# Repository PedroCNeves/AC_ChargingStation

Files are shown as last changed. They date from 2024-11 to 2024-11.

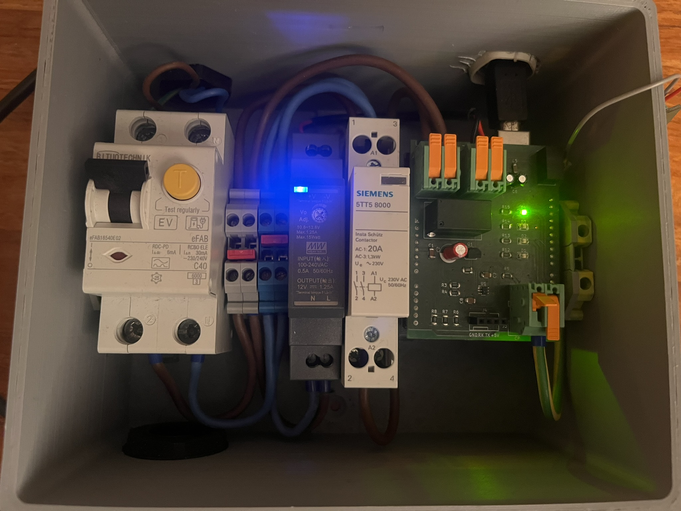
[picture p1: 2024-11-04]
EVSE_Photo.JPEG

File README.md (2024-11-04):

This is a repository for a learning and development project (not a finished product).
This repository contains:
- Code for Arduino Uno to work as an EV AC Charging Station.
- KiCAD Schematic and PCB of a Shield for Arduino Uno to make the hardware for an EV AC Charging Station.
- Gerber files to fabricate the Shield.
- BOM to assemble the Shield.

Instructions to execute this learning project: https://www.udemy.com/course/electric-vehicle-charging-from-theory-to-practice/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

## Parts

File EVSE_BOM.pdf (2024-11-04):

Charging Station Components Link to Product Quantity Unit Cost Sum Cost Box with DIN rail 1 32 32
RCBO https://ecoharmony.co.uk/collecti 1 61 61 Arduino Uno https://store.arduino.cc/products/1 30 30 Charging Station shield for Arduino 1 30 30 DIN Rail adapter for Arduino Uno 1 5 5 Contactor 1P, 20 A https://www.reichelt.nl/nl/nl/insta-1 22 22 DIN Rail Power Supply +12 V https://www.reichelt.nl/nl/nl/schak 1 12 12 Wire 2.5 mm2, blue https://www.elektramat.nl/heluka 1 0.5 0.5 Wire 2.5 mm2, brown https://www.elektramat.nl/heluka 1 0.5 0.5 Wire 2.5 mm2, yellow/green https://www.elektramat.nl/heluka 1 0.5 0.5 Ferrule terminals https://www.elektramat.nl/weidm 25 0.1 2.5 DIN Connectors PE https://www.elektramat.nl/phoeni 2 4 8 DIN Connector Blue https://www.elektramat.nl/phoeni 2 1.2 2.4 DIN Connector Grey https://www.elektramat.nl/phoeni 2 1.2 2.4 Shunt for DIN connectors https://www.elektramat.nl/phoeni 2 0.5 1 End cap for DIN connectors https://www.elektramat.nl/phoeni 2 0.6 1.2 Grommet M20 https://www.elektramat.nl/jacob-w 2 0.6 1.2 Grommet nut M20 https://www.elektramat.nl/jacob-w 2 0.1 0.2 Installation cable 3G2.5 https://www.elektramat.nl/neopre 3 2.4 7.2 Type-2 vehicle connector with cable https://evchargeplus.com/produc 1 170 170
| Total 389.6

Arduino Uno Shield PCB Components (not counting the PCB itself)
Component | Reference in PCB | Link to Product | Quantity | Unit Cost | Sum Cost
Total | 16.595
Operational Amplifier TLV1805DBVR | U1 | 1 | 0.81 | 0.81
Power Supply NKE1212SC | U2 | 1 | 6.2 | 6.2
0.1 uF Capacitors | C1,C3,C5,C7,C8 | 5 | 0.093 | 0.465
10 uF Capacitors | C4,C6 | 2 | 0.12 | 0.24
100 uF Capacitor | C2 | 1 | 0.13 | 0.13
LEDs | D1,D2,D3,D4 | 4 | 0.2 | 0.8
Transistor | Q1 | 1 | 0.4 | 0.4
Relays | K1 | 1 | 1.66 | 1.66
Power Connectors | J1,J2,J3 | 3 | 1.31 | 3.93
Connector, serial coms | J4 | 1 | 0.31 | 0.31
Resistors 1k | R2,R5,R12,R13,R14,R15 | 6 | 0.09 | 0.54
Resistors 100k | R3,R4,R8 | 3 | 0.09 | 0.27
Resistor 300k | R6 | 1 | 0.09 | 0.09
Resistor 220k | R7 | 1 | 0.09 | 0.09
Arduino header 8p | Arduino Uno | 2 | 0.15 | 0.3
Arduino header 6p | Arduino Uno | 1 | 0.16 | 0.16
Arduino header 10p | Arduino Uno | 1 | 0.2 | 0.2

https://nl.mouser.com/ProductDetahttps://www.reichelt.nl/nl/nl/index.hhttps://nl.mouser.com/ProductDetahttps://nl.mouser.com/ProductDetahttps://nl.mouser.com/Product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

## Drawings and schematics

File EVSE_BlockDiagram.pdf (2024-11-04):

## EVSE V2

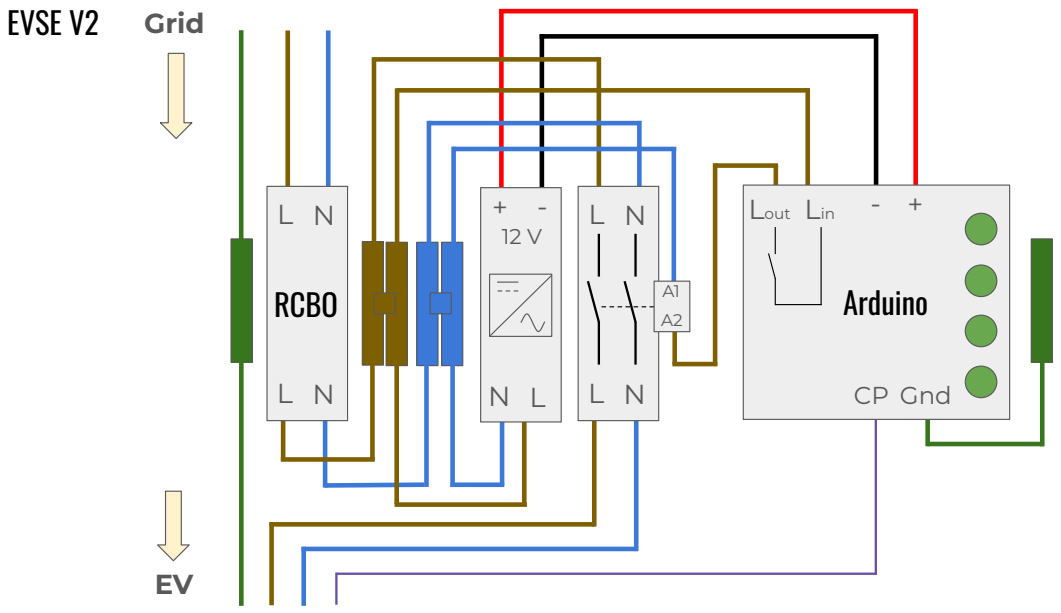
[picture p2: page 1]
RCBO; Grid; Arduino; Lout Lin; CP Gnd

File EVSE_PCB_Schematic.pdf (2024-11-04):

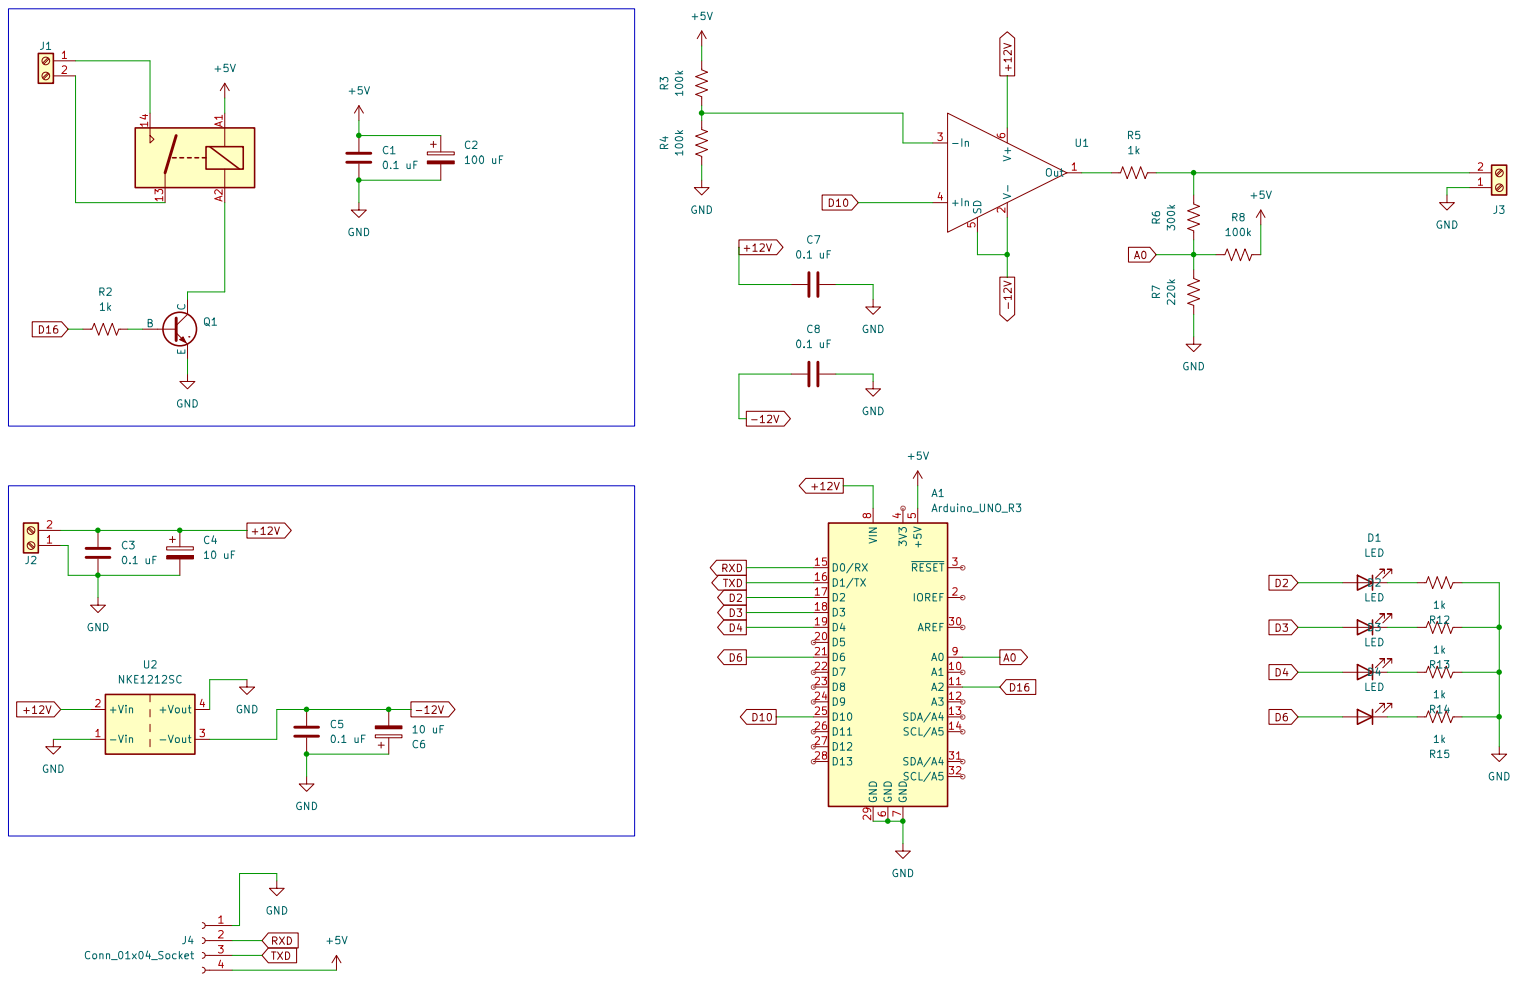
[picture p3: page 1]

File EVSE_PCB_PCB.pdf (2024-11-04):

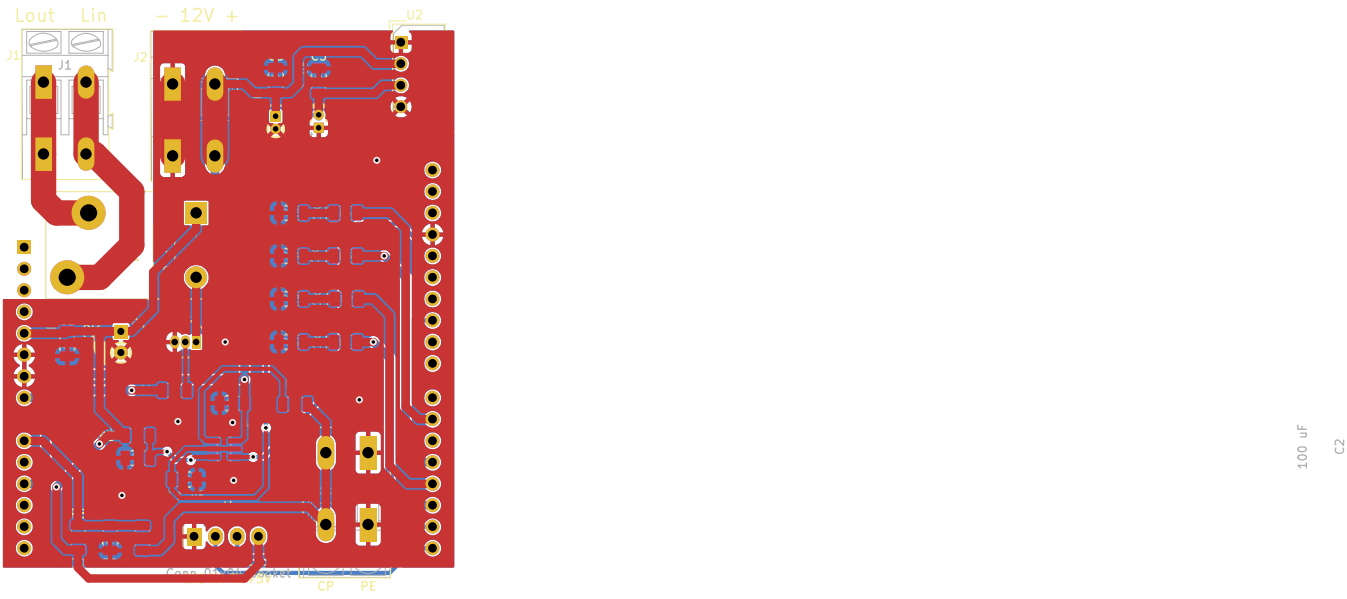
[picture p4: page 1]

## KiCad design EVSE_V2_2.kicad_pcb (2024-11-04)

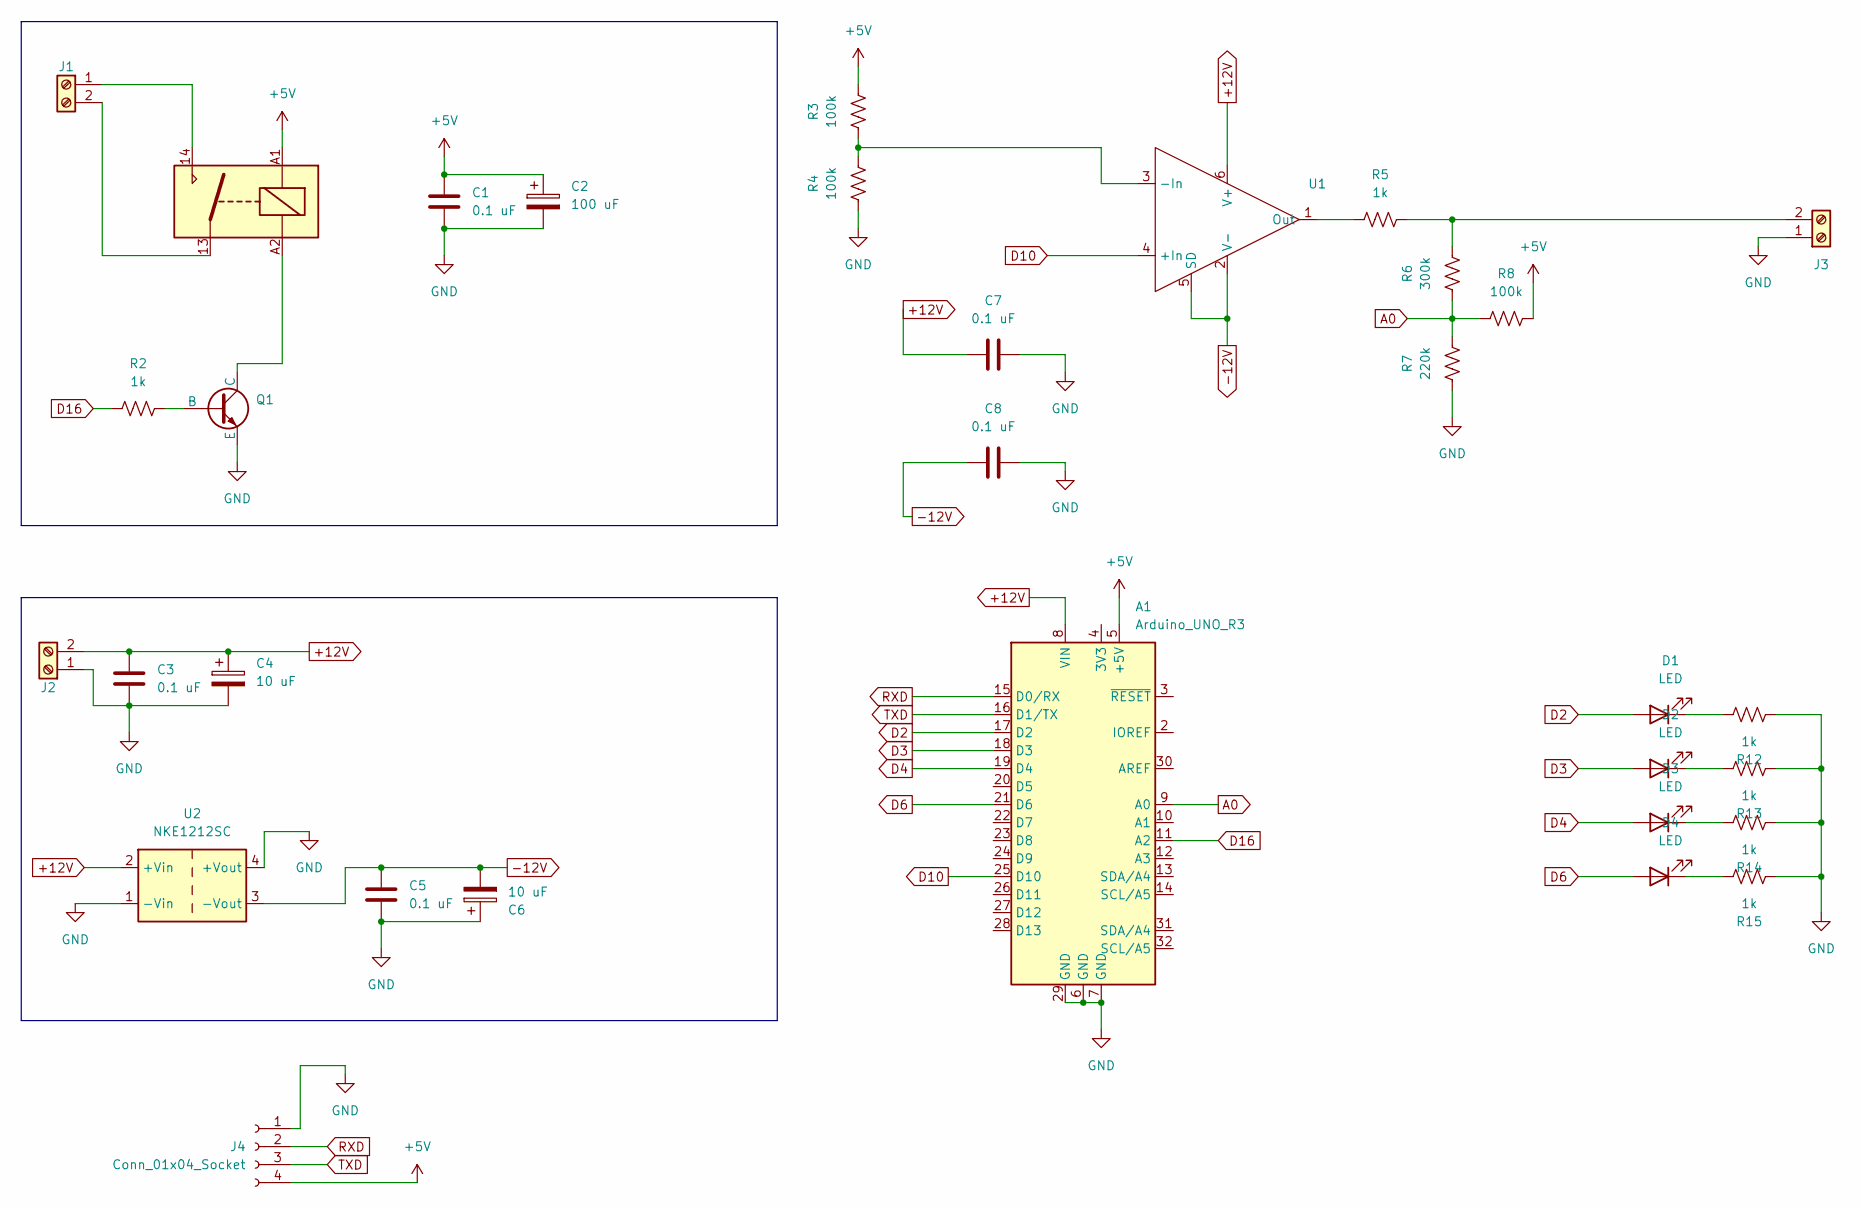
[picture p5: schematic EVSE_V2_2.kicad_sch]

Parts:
A1: Arduino_UNO_R3
C1, C3, C5, C7, C8: 0.1 uF; C_1206_3216Metric
C2: 100 uF; CP_Radial_D6.3mm_P2.50mm
C4, C6: 10 uF; CP_Radial_D4.0mm_P1.50mm
D1, D2, D3, D4: LED; LED_1206_3216Metric
J1, J2, J3: Screw_Terminal_01x02; Lever 2 - 2,5 2-5,0
J4: Conn_01x04_Socket; FanPinHeader_1x04_P2.54mm_Vertical
K1: Relay_SPST-NO; Relay_TE_SPST_16A
Q1: NPN; TO-92_3
R2, R5, R12, R13, R14, R15: 1k; R_1206_3216Metric
R3, R4, R8: 100k; R_1206_3216Metric
R6: 300k; R_1206_3216Metric
R7: 220k; R_1206_3216Metric
U1: SOT-23-6
U2: NKE1212SC

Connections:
+5V: A1.5 (+5V), C1.1, C2.1, J4.4, K1.A1, R3.2, R8.2
+12V: A1.8 (VIN), C3.1, C4.1, C7.1, J2.2, U1.6 (V+), U2.2 (+Vin)
-12V: C5.1, C6.2, C8.1, U1.2 (V-), U1.5 (SD), U2.3 (-Vout)
A0: A1.9 (A0), R6.1, R7.2, R8.1
D2: A1.17 (D2), D1.2 (A)
D3: A1.18 (D3), D2.2 (A)
D4: A1.19 (D4), D3.2 (A)
D6: A1.21 (D6), D4.2 (A)
D10: A1.25 (D10), U1.4 (+In)
D16: A1.11 (A2), R2.1
GND: A1.6 (GND), A1.7 (GND), A1.29 (GND), C1.2, C2.2, C3.2, C4.2, C5.2, C6.1, C7.2, C8.2, J2.1, J3.1, J4.1, Q1.3 (E), R4.1, R7.1, R12.1, R13.1, R14.1, R15.1, U2.1 (-Vin), U2.4 (+Vout)
unnamed: D1.1 (K), R12.2
unnamed: D2.1 (K), R13.2
unnamed: D3.1 (K), R14.2
unnamed: D4.1 (K), R15.2
unnamed: J1.1, K1.14
unnamed: J1.2, K1.13
unnamed: J3.2, R5.2, R6.2
unnamed: Q1.2 (B), R2.2
unnamed: K1.A2, Q1.1 (C)
unnamed: R3.1, R4.2, U1.3 (-In)
unnamed: R5.1, U1.1 (Out)
RXD: A1.15 (D0/RX), J4.2
TXD: A1.16 (D1/TX), J4.3

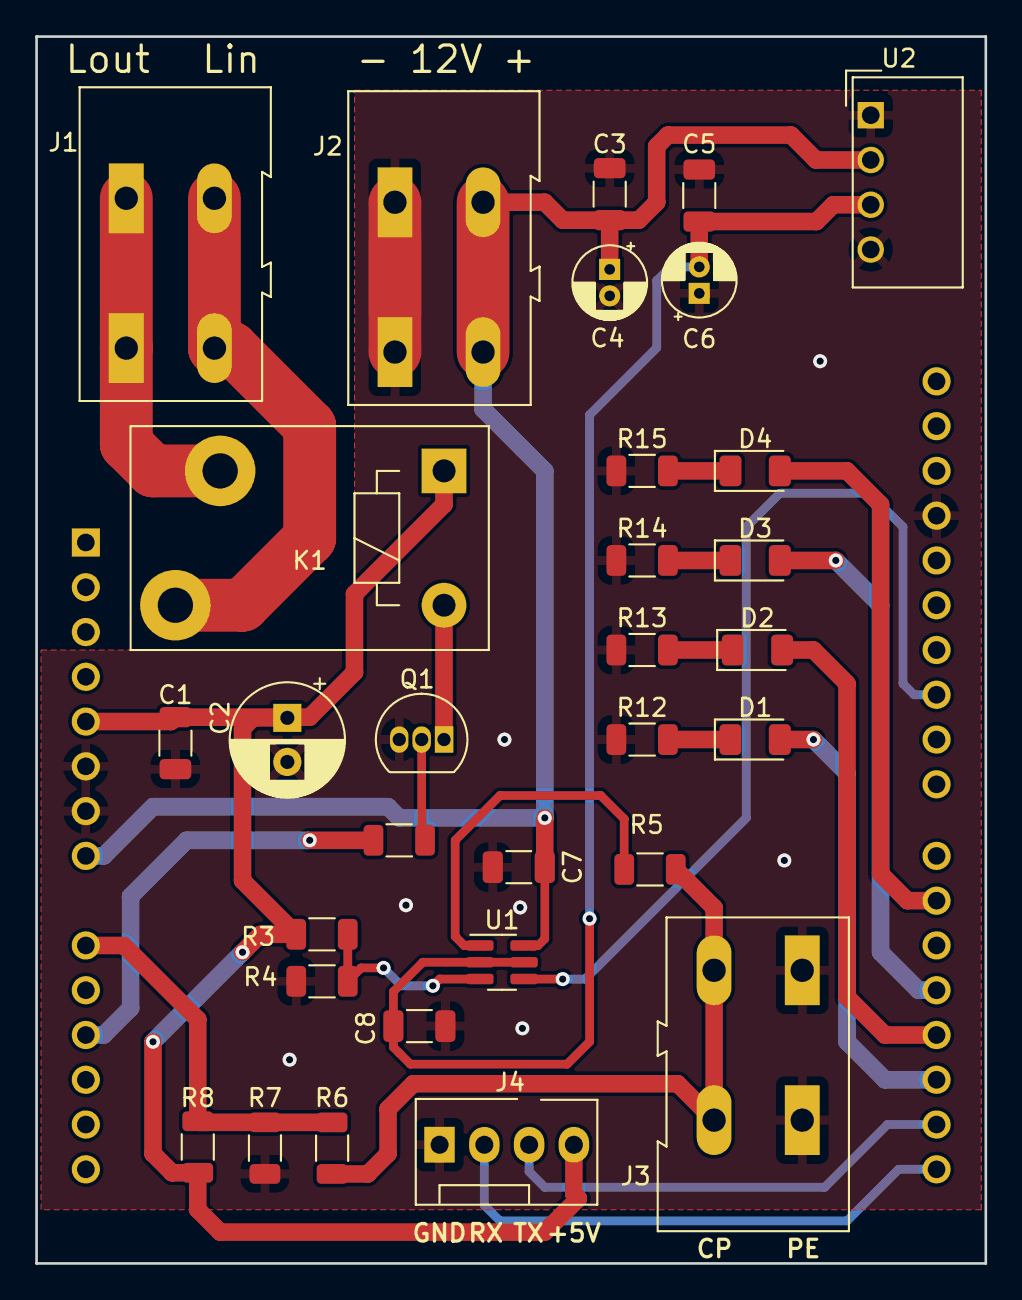
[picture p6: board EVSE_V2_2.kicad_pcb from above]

Board: 2 copper layers, 53.8 x 69.6 mm, 32 parts (1 on the bottom side), 24 nets.

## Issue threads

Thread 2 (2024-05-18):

Adapt to ESP8266 and become an IoT Charger

fryefryefrye, 2024-05-18:
Use case:
1: Start/Stop charging process with Smartphone.
2: Adjust the power of EV charging with Smartphone.
3: Adjust the power of EV charging automatically based on the Power Consumption of your home, maximum charging your EV without affecting the household use.

Background:

I have built a Wi-Fi/4G power monitor and On/Off module， and use it for a while.
It used for control and monitor my EV charging process.
But I always want to have the ability to control the power of charging, not only on/off.
I know the CP single is using for that, but I do not know how to control a PWM wave with +12v/-12v.
With the help of your project, I can do it now. Thank you very much.
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

Adapt to ESP8266 D1 Mini board.

ESP8266 is an 3.3v CPU.
ESP8266 have only one Analog input accept 0 -1v.
There is an 1/3 voltage divider integrated into the ESP8266 D1 board.
So, some modification is need.
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

jarno83, 2024-05-27:
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

Hi, you have a full project source somewhere? Thanks.

fryefryefrye, 2024-05-27:
> Hi, you have a full project source somewhere? Thanks.

For communication code, I use a platform built by myself, which has no reference value.
The code for the EVSE part is almost the same as for the main project, with only some ADC values to be modified.

PedroCNeves, 2024-05-27:
Thank you very much for the contribution! Indeed, I plan to have the Charging Station connected one day. I'll leave this issue open until it is connected.

fryefryefrye, 2024-05-27:
> Thank you very much for the contribution! Indeed, I plan to have the Charging Station connected one day. I'll leave this issue open until it is connected.

You are missing Power Meter Function on your board.
I highly recommend using this one I have used, it is more safe，easy to use, and accurate.
https://www.aliexpress.us/item/3256806146671454.html

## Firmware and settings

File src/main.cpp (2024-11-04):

#include <Arduino.h>
#include "PWM.h"

#define CP_OUT 10 // Setting Arduino pin 10 as output - Control Pilot signal generator
#define CP_IN A0 // Setting Arduino pin A0 as input - Control Pilot signal reader

int counter = 0; // Initialize counter for debug messages over the serial port
int counter2 = 0; // Initialize counter for LED blinking when charging

float cp_pwm = 255; // Initialize the PWM value for the Control Pilot signal generator (255 = flat positive signal)
int frequency = 1000; // Initialize the frequency of the PWM signal (1 kHz)
// Initialize the PWM value for the Control Pilot signal generator when charging 
// Example: Set to 10 A -> Duty Cycle = 10/0.6 = 16.67% -> 255 * 0.1667 = 42.5
// Example: Set t0 16 A -> Duty Cycle = 16/0.6 = 26.66% -> 255 * 0.266 = 68.3
float cp_pwm_charging = 42; // (42 = 10 A)

int findPeakVoltage();  // Function prototype for finding the peak voltage read by pin A0 and determine the charging state (A, B, C, F)
int peak_voltage = 0; // Initialize the peak voltage read by pin A0
int current_voltage = 0; // Initialize the current voltage read by pin A0

char state = 'a'; // Initialize the charging state (A, B, C, F)
int charging = 0; // Initialize the charging state (0 = not charging, 1 = charging)

void setup() {
  // Set up the serial port. This is useful for debugging
  Serial.begin(9600); // Set the baud rate to 9600 bps

  // Set up the PWM
  InitTimersSafe();
  bool success = SetPinFrequencySafe(CP_OUT, frequency); // Set the frequency of the PWM signal to 1 kHz
  if(success) {
    pinMode(CP_OUT, OUTPUT); // Set the CP_OUT pin as output
    pwmWrite(CP_OUT, 255); // Set the CP_OUT pin to +12V
  }

  // Set up the LED pins as output
  pinMode(4, OUTPUT);
  pinMode(6, OUTPUT);
  pinMode(2, OUTPUT);
  pinMode(3, OUTPUT);

  // Set the Relay pin as output
  pinMode(16, OUTPUT);

  // Initialize Relay and LEDs states
  digitalWrite(16, LOW); // Relays open
  digitalWrite(6, HIGH); // Top LED on
  digitalWrite(2, LOW); // Bottom LED off
}

void loop() {
  counter++;
  if (counter > 10) {
    counter = 0;
    Serial.println("Counter = 10");
    Serial.print("Peak Voltage: ");
    Serial.println(peak_voltage);
    Serial.println(state);
  }
  if (charging == 1) {
    counter2++;
    if (counter2 > 10) {
      counter2 = 0;
      // Blink the middle LEDs when charging
      if (digitalRead(3) == HIGH) {
        digitalWrite(3, LOW);
        digitalWrite(4, HIGH);
      }
      else {
        digitalWrite(3, HIGH);
        digitalWrite(4, LOW);
      }
    }
  }
  
  // Read the CP voltage peaks
  findPeakVoltage();

  // Set the charging state based on the peak voltage
  if (peak_voltage > 970) {
    //state A
    state = 'a';
    charging = 0;
    pwmWrite(CP_OUT, 255); // CP set to fixed +12V
    digitalWrite(16, LOW); // Relays open
    digitalWrite(2, LOW); // Bottom LED off
    digitalWrite(3, LOW); // Middle d LED off
    digitalWrite(4, LOW); // Middle u LED off
  }
  else if (peak_voltage > 870) {
    //state B
    state = 'b';
    charging = 0;
    pwmWrite(CP_OUT, cp_pwm_charging); // Exanple 10 A -> Duty Cycle = 10/0.6 = 16.67% -> 255 * 0.1667 = 42.5
    digitalWrite(16, LOW); // Relays open
    digitalWrite(2, HIGH); // Bottom LED on
    digitalWrite(3, LOW); // Middle d LED off
    digitalWrite(4, LOW); // Middle u LED off
  }
  else if (peak_voltage > 780) {
    //state C
    state = 'c';
    charging = 1;
    pwmWrite(CP_OUT, cp_pwm_charging); // Exanple 10 A -> Duty Cycle = 10/0.6 = 16.67% -> 255 * 0.1667 = 42.5
    digitalWrite(16, HIGH); // Relays closed
    digitalWrite(2, HIGH); // Bottom LED on
  }
  else {
    //state F
    state = 'f'; // CP set to fixed -12V
    charging = 0;
    pwmWrite(CP_OUT, 0);
    digitalWrite(16, LOW); // Relays open
    digitalWrite(2, LOW); // Bottom LED off
    digitalWrite(3, LOW); // Middle d LED off
    digitalWrite(4, LOW); // Middle u LED off
  }



}

// function that finds the peak voltage read by pin A0
  int findPeakVoltage() {
    int i = 0;
    current_voltage = 0;
    peak_voltage = 0;
    while (i < 1000) {
      current_voltage = analogRead(CP_IN);
      if (current_voltage > peak_voltage) {
        peak_voltage = current_voltage;
      }
      i++;
    }
    return peak_voltage;
  }

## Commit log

2024-04-18 Added v1 of all resource files
    [9_3_EVSE.kicad_pcb, 9_3_EVSE.kicad_sch, 9_4_Arduino_Fix.stl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]
2024-11-04 This Commit contains the code more organized and the second version of the Arduino Uno shield. This version outsources the power connection to an external contactor.
    [9_3_EVSE.kicad_pcb, 9_3_EVSE.kicad_sch, 9_4_Arduino_Fix.stl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]
